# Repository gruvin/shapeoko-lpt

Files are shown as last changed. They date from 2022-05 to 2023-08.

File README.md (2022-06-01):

# Shapeoko UCCNC Upgrade

### Replacing [Shapeoko Pro XL](https://shop.carbide3d.com/collections/machines/products/shapeoko-pro-cnc-router?variant=33007028797501) basic stepper drivers and ditching GRBL in favour of advanced [UCCNC](https://cncdrive.com/UCCNC.html) Controller, using [UC100](https://cncdrive.com/UC100.html) USB interface to plug into this board.

## Why?

Mostly because I really like being able to pause, rewind, start, stop and see toolpaths in realtime. Call me old fashion. 

As a bonus, we get waaaaaay smoother, faster and generally more reliable stepper motors, using "proper" drivers.

## Features

Firstly, I didn't want to cut any wires ...

- Uses original Carbide3D Shapeoko power brick 24VDC @ 5A. (MOSFET switch and onboard 5V supply should handle double that V/A no problem.)
- Uses all original Shapeoko connectors for Power Switch (with blue LED), End Stops, BitSetter & BitZero. (An adapter board for the stepper motors is coming. The latter will be one each for the motor outputs on the stepper drivers.)

... etcetera ...
- Connects to your choice of "decent" stepper drivers

- Provides 24VDC/5A Charge Pump Switched power for drivers. Each of X/Y/Z ports has +5V/STEP/DIR/EN outputs (active low and Y1/Y2 are wired in parrallel or series. Your chpoice.)

- Built-in safety "charge pump" prevents 24VDC coming live until UCCNC is up and ready on the PC (can be bypassed with jumper.)

- VFD Spindle control with 0-10V speed control

- External 3 relay connector (4 if no charge pump). Relay 1 of 4 operates from EN (stepper enable). Relay 2 and 3 are connected to LPT P8 and P9 (Flood/Mist/Vacuum/Air.)

- Onboard 5VDC 1A supply.

- Input for **!! EMMERGENCY STOP !!** (normally closed switch.) Currently, the signal just goes to LPT P1, for your controller software (USCNC/Mach3) to deal with. Can use for that or Feed Hold if preferred.

## Status
### 2022-06-02 

First batch of assembled prototype PCBs were a bust due to both errors and having been obsoleted by lots of design changes since ordering them.

Trying to get a full week without making any chages before ordering a set of V2.0.

### KiCAD sneak peek, very much a work in progress ...

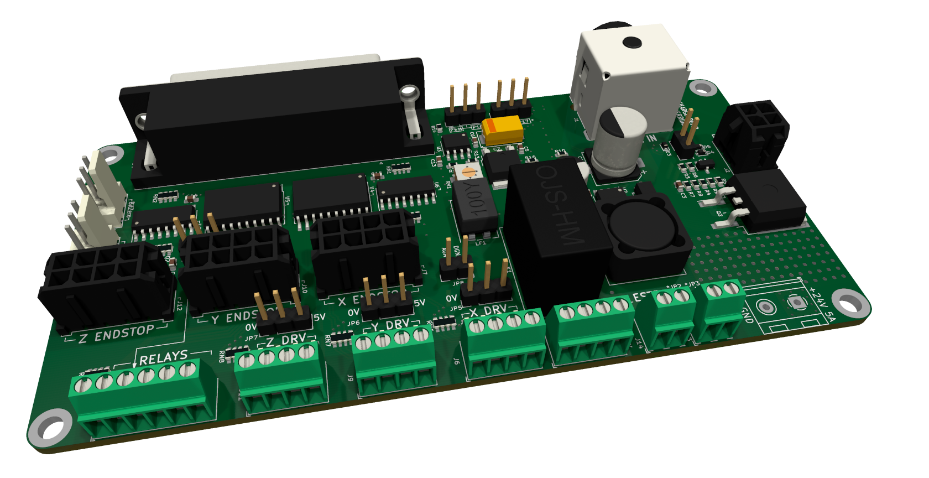
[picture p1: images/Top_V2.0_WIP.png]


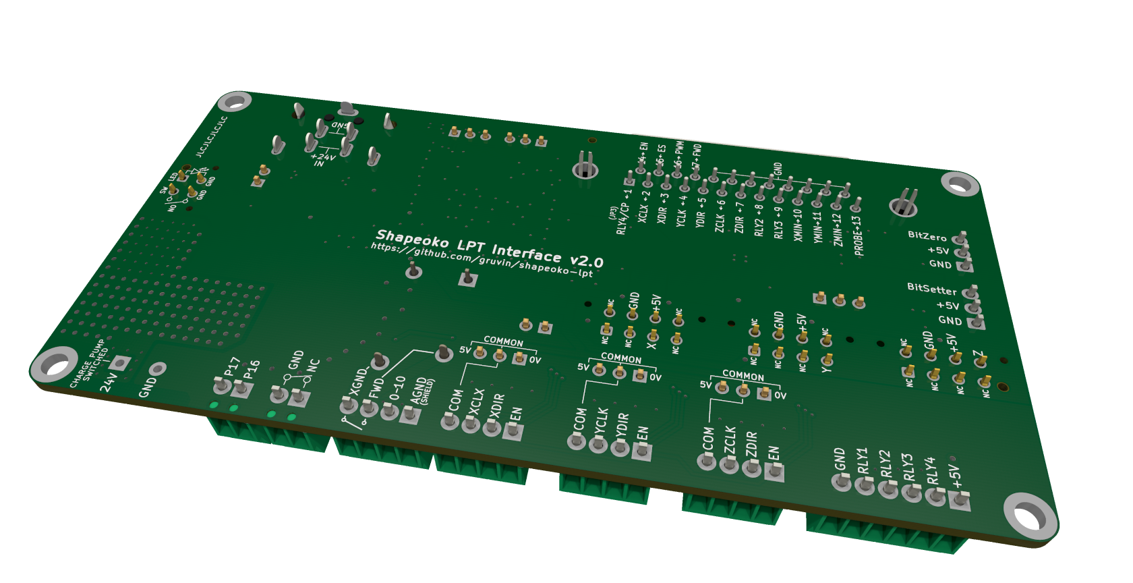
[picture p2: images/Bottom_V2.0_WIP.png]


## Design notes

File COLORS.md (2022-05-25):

# KiCAD 3D Viewer Custom Colors

## Solder Mask

### Purple
#370F80E7

### Emerald Green
#104624F7

## Other
Copper
#D99A6FFF

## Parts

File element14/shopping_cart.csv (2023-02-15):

Line No. | Order Code | Your Part No | Qty | Mfr Part No | Manufacturer Name | Manufacturer / Description | Availability | Unit Price (excl GST) | Line Price (excl GST)
1 | 1012247 |  | 5.0 | 43045-0412 | MOLEX | MOLEX Pin Header, With Polarizing Peg, Power, 3 mm, 2 Rows, 4 Contacts, Through Hole Straight | 30024 | 1.8900 | 9.45
2 | 1654450 |  | 3.0 | 43045-0814 | MOLEX | MOLEX Pin Header, Power, 3 mm, 2 Rows, 8 Contacts, Through Hole Straight, Micro-Fit 3.0 43045 | 4410 | 4.6500 | 13.95
3 | 2839851 |  | 1.0 | KPJX-4S-S | KYCON | KYCON High Power Connector, Through Hole, KPJX, Receptacle, 48 VDC, 7.5 A, PCB Mount, Through Hole | 3085 | 2.5900 | 2.59
4 | 2646350 |  | 1.0 | IRF9540SPBF | VISHAY | VISHAY Power MOSFET, P Channel, 100 V, 19 A, 0.2 ohm, TO-263AB, Surface Mount | 1484 | 4.3800 | 4.38
5 | 2527547 |  | 10.0 | CTBP5000/2 | CAMDENBOSS | CAMDENBOSS Wire-To-Board Terminal Block, 5 mm, 2 Ways, 22 AWG, 14 AWG, 1.5 mm², Screw | 5179 | 0.5280 | 5.28
6 | 2799102 |  | 1.0 | MAX5035BUSA+T | MAXIM INTEGRATED / ANALOG DEVICES | MAXIM INTEGRATED / ANALOG DEVICES Buck (Step Down), Switching Regulator, Fixed, 7.5V to 76V In, 5V/1A Out, 125kHz, NSOIC-8 | 5 | 6.1300 | 6.13
7 | 1635912 |  | 2.0 | 74477120 | WURTH ELEKTRONIK | WURTH ELEKTRONIK Power Inductor (SMD), 100 µH, 1.53 A, Shielded, 1.7 A, WE-PD, 12mm x 12mm x 6mm | 7979 | 3.3300 | 6.66
8 | 2836989 |  | 1.0 | MAL218397104E3 | VISHAY | VISHAY Hybrid Aluminium Electrolytic Capacitor, 68 µF, ± 20%, 50 V, Radial Can - SMD, 0.03 ohm | 1430 | 7.1500 | 7.15
9 | 2611386 |  | 2.0 | MCVVT035M221FB3L | MULTICOMP PRO | MULTICOMP PRO SMD Aluminium Electrolytic Capacitor, Radial Can - SMD, 220 µF, 35 V, 2000 hours @ 105°C, Polar | 504 | 0.3880 | 0.78
10 | 2507732 |  | 2.0 | EEEFK1V680SP | PANASONIC | PANASONIC SMD Aluminium Electrolytic Capacitor, Radial Can - SMD, 68 µF, 35 V, 0.36 ohm, 2000 hours @ 105°C | 4855 | 0.9200 | 1.84
11 | 2611399 |  | 5.0 | MCVVT050M221GB3L | MULTICOMP PRO | MULTICOMP PRO SMD Aluminium Electrolytic Capacitor, Radial Can - SMD, 220 µF, 50 V, 2000 hours @ 105°C, Polar | 2886 | 0.5480 | 2.74
12 | 1709948 |  | 20.0 | MC0603B103M500CT | MULTICOMP PRO | MULTICOMP PRO CERAMIC CAPACITOR 0.01UF, 50V, X7R, 20%, 0603 | 9703 | 0.0450 | 0.90
13 | 9402080 |  | 20.0 | CC0603KRX5R6BB105 | YAGEO | YAGEO SMD Multilayer Ceramic Capacitor, 1 µF, 10 V, 0603 [1608 Metric], ± 10%, X5R, CC Series | 918203 | 0.0270 | 0.54
14 | 432210 |  | 20.0 | CC0603KRX7R7BB104 | YAGEO | YAGEO SMD Multilayer Ceramic Capacitor, 0.1 µF, 16 V, 0603 [1608 Metric], ± 10%, X7R, CC Series | 695378 | 0.0300 | 0.60
15 | 3407110 |  | 10.0 | RRE07VSM6STR | ROHM | ROHM Small Signal Diode, Single, 600 V, 700 mA, 1.1 V, 2 A | 2850 | 0.6240 | 6.24

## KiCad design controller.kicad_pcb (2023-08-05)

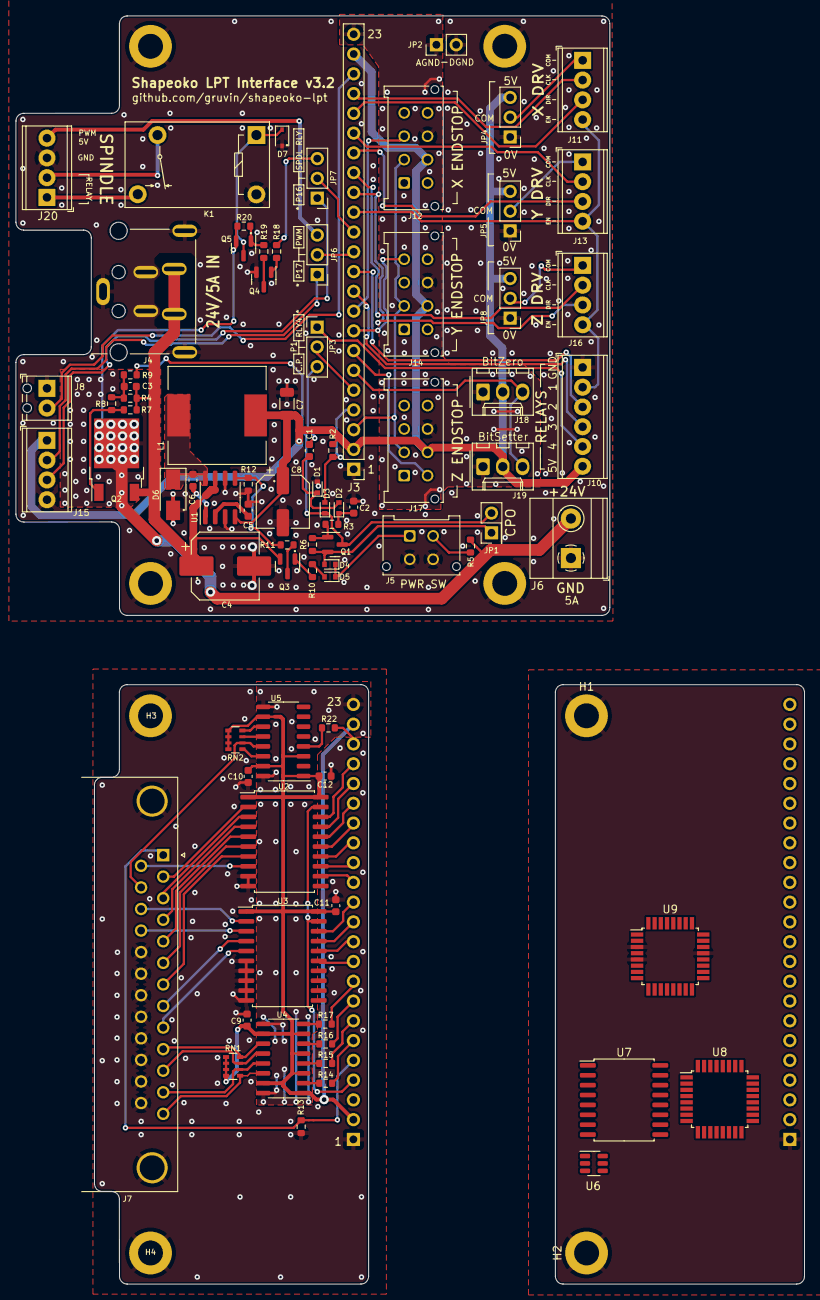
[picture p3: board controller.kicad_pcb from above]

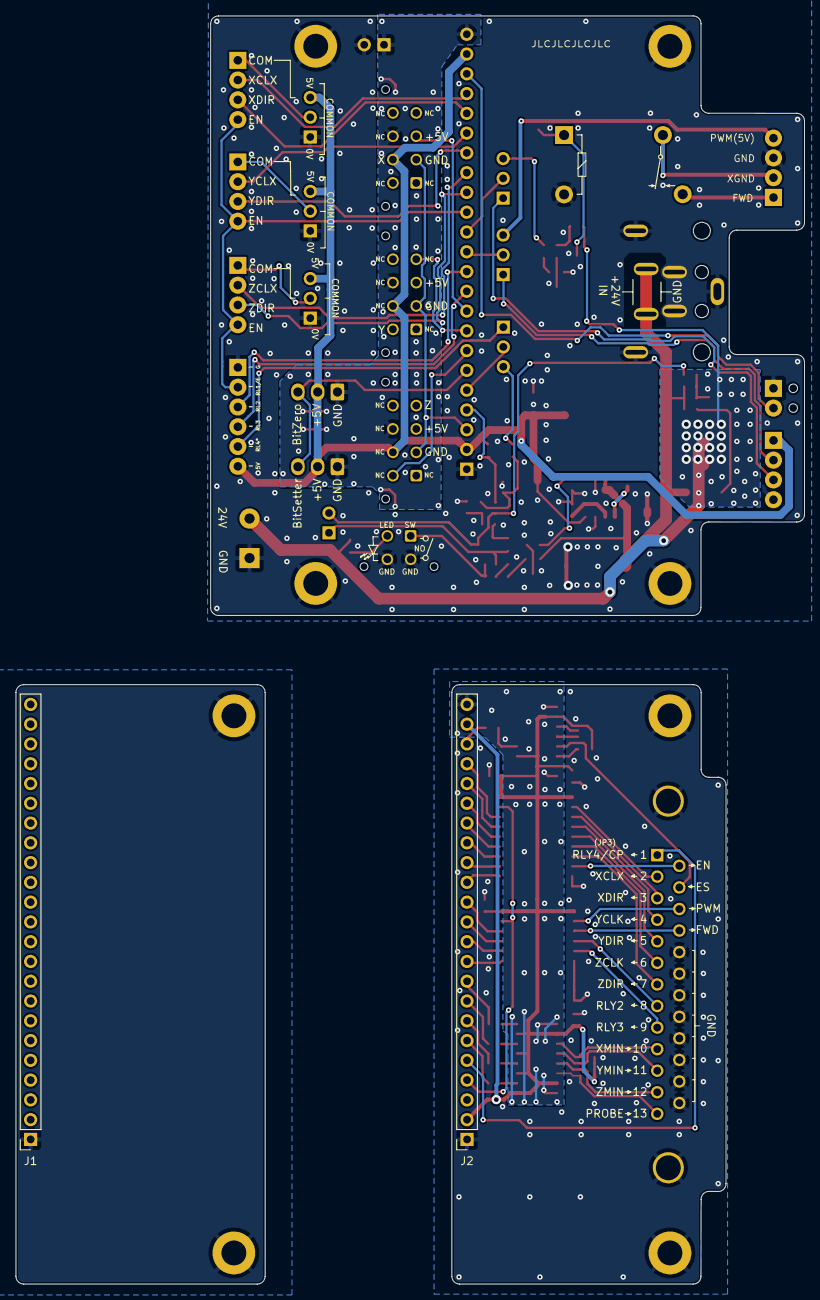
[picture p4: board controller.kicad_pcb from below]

Board: 2 copper layers, 101.3 x 162.9 mm, 100 parts (6 on the bottom side), 126 nets.

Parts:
C1, C5, C6, C9, C10, C11, C12: 100n/50V; C_0603_1608Metric
C2, C3: 1u/50V; C_0603_1608Metric
C4: 100u/35V; CP_Elec_8x10.5_DOT
C7: 22u/25V; C_1206_3216Metric
C8: 68u/35V; CP_Elec_6.3x7.7_DOT
D1, D2, D3, D4, D5: SDM20U40-7; D_SOD-523
D6: SS24A+; D_SMA_DOT
D7: BAT54JFILM; D_SOD-323_DOT
H1, H2, H3, H4, H5, H6, H7, H8: MountingHole_Pad; MountingHole_3.2mm_M3_ISO14580_Pad
J1, J2: Conn_01x06_Female; PinSocket_1x23_P2.54mm_Vertical
J3: Conn_01x022_Male; PinHeader_1x23_P2.54mm_Vertical
J4: KYCON_KPJX-4S-S
J5: MicroFit_2x02; Molex_Micro-Fit_3.0_43045-0412_2x02_P3.00mm_Vertical
J6: 24V/5A OUT; TerminalBlock_Phoenix_MKDS-1,5-2-5.08_1x02_P5.08mm_Horizont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
J7: DB25 FEMALE; DSUB-25_Male_Horizontal_P2.77x2.84mm_EdgePinOffset7.70mm_Ho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
J8: Phoenix MPT; TerminalBlock_Phoenix_MPT-0,5-2-2.54_1x02_P2.54mm_Horizontal
J10: Phoenix MPT; TerminalBlock_Phoenix_MPT-0,5-6-2.54_1x06_P2.54mm_Horizontal
J11, J13, J16, J20: Phoenix MPT; TerminalBlock_Phoenix_MPT-0,5-4-2.54_1x04_P2.54mm_Horizontal
J12, J14, J17: MicroFit_2x04; Molex_Micro-Fit_3.0_43045-0812_2x04_P3.00mm_Vertical
J15: JST_B2B-XH; TerminalBlock_Phoenix_MPT-0,5-4-2.54_1x04_P2.54mm_Horizontal
J18, J19: MLX_1x03; Molex_KK-254_AE-6410-03A_1x03_P2.54mm_Vertical
JP1: Jumper_2; PinHeader_2x01_P2.54mm_Vertical
JP2: GND_ISO; PinHeader_1x02_P2.54mm_Vertical
JP3, JP6, JP7: 1x03_2.54; PinHeader_1x03_P2.54mm_Vertical
JP4, JP5, JP8: Jumper_3; PinHeader_1x03_P2.54mm_Vertical
K1: OJS-SH-124HMF; Relay_SPST_OJS_24V_10A
L1: 100uH 1.5A+; L_12x12mm_H6mm
NT1: NetTie_2; NetTie-2_SMD_Pad0.3mm
NT22, NT25, NT26, NT27: DNI; NetTie-2_SMD_Pad0.3mm
NT23, NT24, NT28: DNI; NetTie-2_SMD_Pad1.0mm
Q1, Q4: BC847; SOT-23
Q2: FDD5614P; TO-252-2
Q3, Q5: BC857; SOT-23_DOT
R2, R7, R11, R13: 1M; R_0603_1608Metric
R3: 6K8; R_0603_1608Metric
R4, R12: 220K; R_0603_1608Metric
R5: 1K; R_0603_1608Metric
R6, R10: 130K; R_0603_1608Metric
R8: 680K; R_0603_1608Metric
R9: 330K; R_0603_1608Metric
R14, R15, R16, R17, R22: 330; R_0603_1608Metric
R18, R19: 5K6; R_0603_1608Metric
R20: 10K; R_0603_1608Metric
RN1, RN2: 1Kx4; R_Array_Convex_4x0603
U1: MAX5035BUSA; SOIC-8_3.9x4.9mm_P1.27mm
U2, U3: 74HC245; SOIC-20W_7.5x12.8mm_P1.27mm
U4, U5: ACSL-6310; SO-16_3.9x9.9mm_P1.27mm
U6: USBLC6-2SC6; SOT-23-6
U7: ADUM4160; SOIC-16W_7.5x10.3mm_P1.27mm
U8: ATmega16U2-A; TQFP-32_7x7mm_P0.8mm
U9: ATmega328P-A; TQFP-32_7x7mm_P0.8mm

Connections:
5V_nEN: D5.2 (A), R10.2
24V_IN: C3.1, C4.1, J4.1, J4.4, NT23.1, Q2.3 (S), R4.1, R7.2
24V_SAFE: J6.2, NT22.2, Q2.2 (D), Q5.2 (E), R20.1
+5V: J3.2, J3.22, J10.6, J12.6, J14.6, J15.1, J17.6, J18.2, J19.2, NT24.2, NT28.2, R2.2
+5VA: C9.1, C10.1, C11.1, C12.1, J1.2, J1.22, J2.2, J2.22, RN1.1 (R1.1), RN1.2 (R2.1), RN1.3 (R3.1), RN1.4 (R4.1), RN2.1 (R1.1), RN2.2 (R2.1), RN2.3 (R3.1), RN2.4 (R4.1), U2.1 (A->B), U2.20 (VCC), U3.1 (A->B), U3.20 (VCC), U4.1 (A1), U4.3 (A2), U4.5 (A3), U4.7 (A4), U4.10 (Vdd), U4.15 (Vdd), U5.1 (A1), U5.3 (A2), U5.5 (A3), U5.7 (A4), U5.10 (Vdd), U5.15 (Vdd), U9.4 (VCC), U9.6 (VCC), U9.18 (AVCC), U9.20 (AREF)
/Connectors & Jumpers/CHARGE_PUMP_OUT: C1.1, JP3.3 (B)
/Connectors & Jumpers/EN_IN: J3.14, J11.4, J13.4, J16.4, NT27.1
/Connectors & Jumpers/ESTOP_OUT: J3.21, J8.2
/Connectors & Jumpers/HOLD_OUT: J3.3, J12.2, J14.2, J17.2
/Connectors & Jumpers/P1_IN: J3.5, JP3.2 (C)
/Connectors & Jumpers/P16_IN: J3.13, JP7.2 (C)
/Connectors & Jumpers/P17_IN: J3.12, JP6.2 (C)
/Connectors & Jumpers/PROBE_OUT: J3.6, J18.3, J19.3
/Connectors & Jumpers/RELAY1: J10.2, NT27.2
/Connectors & Jumpers/RELAY2: J10.3, NT26.2
/Connectors & Jumpers/RELAY2_IN: J3.11, NT26.1
/Connectors & Jumpers/RELAY3: J10.4, NT25.2
/Connectors & Jumpers/RELAY3_IN: J3.10, NT25.1
/Connectors & Jumpers/RELAY4: J10.5, JP3.1 (A)
/Connectors & Jumpers/STP_5V: JP4.3 (B), JP5.3 (B), JP8.3 (B), NT28.1
/Connectors & Jumpers/VFD_FWD: J20.2, K1.5
/Connectors & Jumpers/VFD_PWM: J20.4, JP6.3 (B)
/Connectors & Jumpers/VFD_XGND: J20.1, K1.3
/Connectors & Jumpers/XCLK_IN: J3.20, J11.2
/Connectors & Jumpers/XDIR_IN: J3.19, J11.3
/Connectors & Jumpers/XMIN_OUT: J3.9, J12.3
/Connectors & Jumpers/X_COM: J11.1, JP4.2 (C)
/Connectors & Jumpers/X_P16_OUT: J15.3, JP7.1 (A)
/Connectors & Jumpers/X_P17_OUT: J15.2, JP6.1 (A)
/Connectors & Jumpers/YCLK_IN: J3.18, J13.2
/Connectors & Jumpers/YDIR_IN: J3.17, J13.3
/Connectors & Jumpers/YMIN_OUT: J3.8, J14.4
/Connectors & Jumpers/Y_COM: J13.1, JP5.2 (C)
/Connectors & Jumpers/ZCLK_IN: J3.16, J16.2
/Connectors & Jumpers/ZDIR_IN: J3.15, J16.3
/Connectors & Jumpers/ZMIN_OUT: J3.7, J17.5
/Connectors & Jumpers/Z_COM: J16.1, JP8.2 (C)
/GRBL Interface/HOLD_IN: J1.3, U9.24 (PC1)
/GRBL Interface/P2_OUT: J1.20, U9.32 (PD2)
/GRBL Interface/P3_OUT: J1.19, U9.9 (PD5)
/GRBL Interface/P4_OUT: J1.18, U9.1 (PD3)
/GRBL Interface/P5_OUT: J1.17, U9.10 (PD6)
/GRBL Interface/P6_OUT: J1.16, U9.2 (PD4)
/GRBL Interface/P7_OUT: J1.15, U9.11 (PD7)
/GRBL Interface/P8_OUT: J1.11, U9.26 (PC3)
/GRBL Interface/P9_OUT: J1.10, U9.27 (PC4)
/GRBL Interface/P10_IN: J1.9, U9.13 (PB1)
/GRBL Interface/P11_IN: J1.8, U9.14 (PB2)
/GRBL Interface/P12_IN: J1.7, U9.16 (PB4)
/GRBL Interface/P13_IN: J1.6, U9.28 (PC5)
/GRBL Interface/P14_OUT: J1.14, U9.12 (PB0)
/GRBL Interface/P15_IN: J1.21, U9.23 (PC0)
/GRBL Interface/P16_OUT: J1.13, U9.17 (PB5)
/GRBL Interface/P17_OUT: J1.12, U9.15 (PB3)
/LPT Interface/P1_IN: J7.1, NT1.1, R13.1
/LPT Interface/P1_OUT: J2.5, NT1.2
/LPT Interface/P2_IN: J7.2, U2.2 (A0)
/LPT Interface/P2_OUT: J2.20, U2.18 (B0)
/LPT Interface/P3_IN: J7.3, U2.3 (A1)
/LPT Interface/P3_OUT: J2.19, U2.17 (B1)
/LPT Interface/P4_IN: J7.4, U2.4 (A2)
/LPT Interface/P4_OUT: J2.18, U2.16 (B2)
/LPT Interface/P5_IN: J7.5, U2.5 (A3)
/LPT Interface/P5_OUT: J2.17, U2.15 (B3)
/LPT Interface/P6_IN: J7.6, U2.6 (A4)
/LPT Interface/P6_OUT: J2.16, U2.14 (B4)
/LPT Interface/P7_IN: J7.7, U2.7 (A5)
/LPT Interface/P7_OUT: J2.15, U2.13 (B5)
/LPT Interface/P8_IN: J7.8, U3.4 (A2)
/LPT Interface/P8_OUT: J2.11, U3.16 (B2)
/LPT Interface/P9_IN: J7.9, U3.5 (A3)
/LPT Interface/P9_OUT: J2.10, U3.15 (B3)
/LPT Interface/P10_IN: J2.9, R17.2
/LPT Interface/P10_OUT: J7.10, RN1.8 (R1.2), U4.11 (O1)
/LPT Interface/P11_IN: J2.8, R16.2
/LPT Interface/P11_OUT: J7.11, RN1.7 (R2.2), U4.12 (O1)
/LPT Interface/P12_IN: J2.7, R15.2
/LPT Interface/P12_OUT: J7.12, RN1.6 (R3.2), U4.13 (O1)
/LPT Interface/P13_IN: J2.6, R14.2
/LPT Interface/P13_OUT: J7.13, RN1.5 (R4.2), U4.14 (O1)
/LPT Interface/P14_IN: J7.14, U2.8 (A6)
/LPT Interface/P14_OUT: J2.14, U2.12 (B6)
/LPT Interface/P15_IN: J2.21, R22.2
/LPT Interface/P15_OUT: J7.15, RN2.6 (R3.2), U5.13 (O1)
/LPT Interface/P16_IN: J7.16, U3.2 (A0)
/LPT Interface/P16_OUT: J2.13, U3.18 (B0)
/LPT Interface/P17_IN: J7.17, U3.3 (A1)
/LPT Interface/P17_OUT: J2.12, U3.17 (B1)
/LPT Interface/nCE_IN: J2.4, U2.19 (CE), U3.19 (CE)
/Power/PLED: J5.2, R5.1
/Power/Q1_B: Q1.1 (B), R3.2, R6.1
/Power/Q1_C: D3.1 (K), JP1.2 (B), Q1.3 (C), R9.2
/Power/Q1_E: D4.2 (A), JP1.1 (A), Q1.2 (E), R6.2
/Power/U2_BST: C6.1, U1.1 (BST)
/Power/U2_FB: C7.2, C8.1, L1.2, NT24.1, U1.4 (FB)
/Power/U2_LX: C6.2, D6.1 (K), L1.1, U1.8 (LX)
/Power/U2_ON_nOFF: R11.1, R12.1, U1.5 (ON/~OFF)
/Power/U2_VD: C5.1, U1.2 (VD)
/Power/U2_VIN: NT23.2, Q3.2 (E), U1.7 (VIN)
/Power/nCE_OUT: D3.2 (A), J3.4, R2.1
GND: C2.2, C4.2, C5.2, C7.1, C8.2, D1.2 (A), D6.2 (A), D7.2 (A), H5.1, H6.1, H7.1, H8.1, J3.1, J4.2, J4.3, J4.SH, J5.3, J5.4, J6.1, J8.1, J10.1, J15.4, J20.3, JP2.2 (B), JP4.1 (A), JP5.1 (A), JP8.1 (A), K1.1, Q4.2 (E), R12.2, U1.3 (SGND), U1.6 (GND)
GND1: C9.2, C10.2, C11.2, C12.2, H1.1, H2.1, H3.1, H4.1, J1.1, J2.1, J7.0 (PAD), J7.18, J7.19, J7.20, J7.21, J7.22, J7.23, J7.24, J7.25, R13.2, U2.9 (A7), U2.10 (GND), U3.6 (A4), U3.7 (A5), U3.8 (A6), U3.9 (A7), U3.10 (GND), U9.3 (GND), U9.5 (GND), U9.21 (GND)
GND2: J1.23, J2.23, U4.9 (GND), U4.16 (GND), U5.9 (GND), U5.16 (GND)
GND3: U7.2 (GND1), U7.8 (GND1)
GNDA: J3.23, J12.7, J14.7, J17.7, J18.1, J19.1, JP2.1 (A)
unnamed: C1.2, D1.1 (K), D2.2 (A)
unnamed: C2.1, D2.1 (K), R3.1
unnamed: C3.2, R4.2, R8.1, R9.1
unnamed: D4.1 (K), D5.1 (K), J5.1
unnamed: D7.1 (K), K1.6, Q5.3 (C)
unnamed: JP7.3 (B), R18.2
unnamed: NT22.1, R5.2
unnamed: Q2.1 (G), R7.1, R8.2
unnamed: Q3.1 (B), R10.1
unnamed: Q3.3 (C), R11.2
unnamed: Q4.1 (B), R18.1
unnamed: Q4.3 (C), R19.2
unnamed: Q5.1 (B), R19.1, R20.2
unnamed: R14.1, U4.2 (C1)
unnamed: R15.1, U4.4 (C2)
unnamed: R16.1, U4.6 (C3)
unnamed: R17.1, U4.8 (C4)
unnamed: R22.1, U5.4 (C2)
unnamed: RN2.8 (R1.2), U5.11 (O1)
unnamed: RN2.7 (R2.2), U5.12 (O1)
unnamed: RN2.5 (R4.2), U5.14 (O1)

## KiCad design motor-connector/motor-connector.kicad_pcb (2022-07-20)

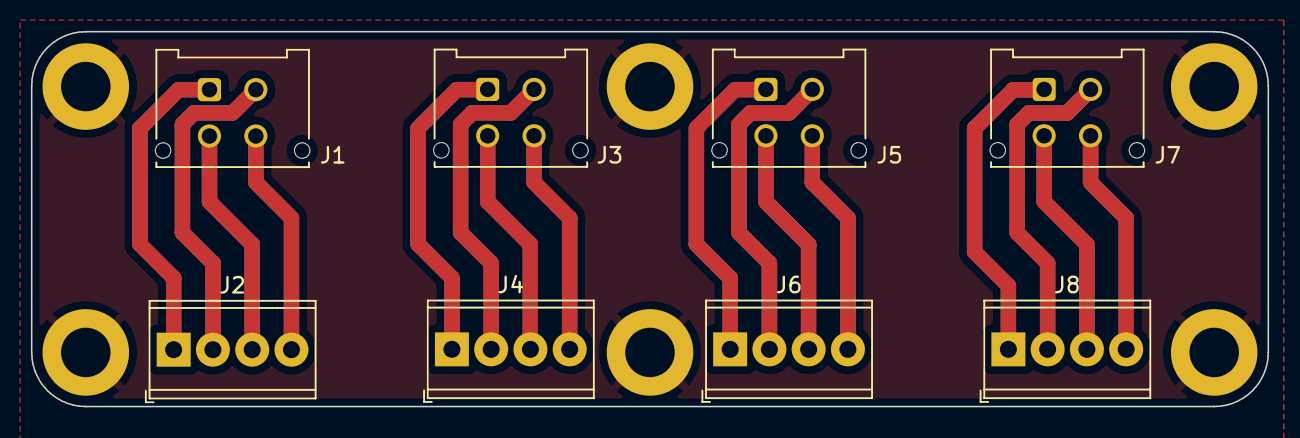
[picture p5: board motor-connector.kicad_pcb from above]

Board: 2 copper layers, 80.0 x 24.2 mm, 14 parts (0 on the bottom side), 17 nets.

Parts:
H1, H2, H3, H4, H5, H6: MountingHole_Pad; MountingHole_3.2mm_M3_DIN965_Pad
J1, J3, J5, J7: Conn_02x02_Top_Bottom; Molex_Micro-Fit_3.0_43045-0412_2x02_P3.00mm_Vertical
J2, J4, J6, J8: Conn_01x04; TerminalBlock_Phoenix_MPT-0,5-4-2.54_1x04_P2.54mm_Horizontal

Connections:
GND: H1.1, H2.1, H3.1, H4.1, H5.1, H6.1
unnamed: J1.1, J2.1
unnamed: J1.2, J2.2
unnamed: J1.3, J2.3
unnamed: J1.4, J2.4
unnamed: J3.1, J4.1
unnamed: J3.2, J4.2
unnamed: J3.3, J4.3
unnamed: J3.4, J4.4
unnamed: J5.1, J6.1
unnamed: J5.2, J6.2
unnamed: J5.3, J6.3
unnamed: J5.4, J6.4
unnamed: J7.1, J8.1
unnamed: J7.2, J8.2
unnamed: J7.3, J8.3
unnamed: J7.4, J8.4

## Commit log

2022-05-14 Much to do about OCD power distribution. (Removed all loop 'antennas' and balanced transmission lines..)
    [controller.kicad_pcb, controller.kicad_sch, power.kicad_sch]
2022-05-14 Some more decoupling caps and routing optimizations.
    [controller.kicad_pcb, controller.kicad_sch, lpt.kicad_sch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]
2022-05-15 Lots of changes and errors fixed. Updated vanity images.
    [conn.kicad_sch, controller.kicad_pcb, controller.kicad_sch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]
2022-05-15 Probe connectors wired wrong. Improved 5V buck reg layout.
    [conn.kicad_sch, controller.kicad_pcb, controller.kicad_sch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]
2022-05-16 Added LEDs (more coming). Changes to charge pump and related power switching.
    [conn.kicad_sch, controller.kicad_pcb, controller.kicad_sch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]
2022-05-16 Forgot R1 and more NT fun.
    [conn.kicad_sch, controller.kicad_pcb, controller.kicad_sch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]
2022-05-17 Resistor networks changed to 0603 'cause JLCPCB has those as 'basic parts' & aunch of tweaks. (WIP)
    [conn.kicad_sch, controller.kicad_pcb, controller.kicad_sch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]
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2022-05-17 Scary file corruption turns out to be just bugs in eschema.
    [conn.kicad_sch, controller.kicad_pcb, controller.kicad_sch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]
2022-05-17 Removed 'Element14' field from all sch/pcb components
    [conn.kicad_sch, controller.kicad_pcb, controller.kicad_sch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]
2022-05-18 Reworked PSU control scheme (schematic only.)
    [conn.kicad_sch, controller.kicad_pcb, controller.kicad_sch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]
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2022-05-18 Change share/_footprints to share/module with new alias '-Project'
    [conn.kicad_sch, controller.kicad_pcb, controller.kicad_sch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]
2022-05-18 Much to do about power
    [conn.kicad_sch, controller.kicad_pcb, controller.kicad_sch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]
2022-05-19 Routed power switching changes.
    [conn.kicad_sch, controller.kicad_pcb, controller.kicad_sch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]
2022-05-19 More power supply and 5A ground return routing optimization.
    [controller.kicad_pcb, controller.kicad_sch, lpt.kicad_sch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]
2022-05-20 Tweaks and JLCPCB LCSC field name changes.
    [conn.kicad_sch, controller.kicad_pcb, controller.kicad_sch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]
2022-05-20 Added 100n extra decoupling cap to PWM 12V reg.
    [conn.kicad_sch, controller.kicad_pcb, controller.kicad_sch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]
2022-05-20 I'm soooo done with this board! :/
    [conn.kicad_sch, controller.kicad_pcb, controller.kicad_sch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]
2022-05-21 Some fixes .... and ... a MAJOR fuck up on the power connector, after the board went into production already.
    [conn.kicad_sch, controller.kicad_pcb, controller.kicad_sch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]
2022-05-21 Corrected unbelievably DUMB ballsup on input power connector.
    [conn.kicad_sch, controller.kicad_pcb, controller.kicad_sch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]
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2022-05-22 More OCD hours really. I need to stop. It's getting stupid. :P
    [controller.kicad_pcb]
2022-05-22 DRC checks. Tagging as V1.0 'actual'
    [conn.kicad_sch, controller.kicad_pcb, controller.kicad_sch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]
2022-05-22 Prepping JLCPCB order for v1.1 assembled boards.
    [controller-B_Cu.gbr, controller-B_Mask.gbr, controller-B_Paste.gbr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]
2022-05-22 JLCPCB Order Placed for JLCPCB_V1.1_FROZEN/.
    [bom-jlcpcb.csv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]
2022-05-23 Lost the top layer ground plane. Got sick of being in Via Hell.
    [conn.kicad_sch, controller.kicad_pcb, controller.kicad_sch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]
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2022-05-24 Unfinished 5V buck routing optimization.
    [controller.kicad_pcb]
2022-05-25 Tweaks & recorded custom 3D Viewer colors.
    [controller.kicad_pcb]
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2022-05-27 Fixed stupid error with LED circuit. (LED are lights, yes but they only turn on when current is going a certain direction. Duh. LOL)
    [conn.kicad_sch, controller.kicad_pcb, controller.kicad_sch]
2022-05-28 Mostly groundplane declutter and loop removal.
    [conn.kicad_sch, controller.kicad_pcb, controller.kicad_sch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]
2022-05-28 More ground plane clearance/optimization.
    [controller.kicad_pcb, power.kicad_sch]
2022-05-29 Moving charge pump 15KHz input closer to source,
    [controller.kicad_pcb, controller.kicad_sch, power.kicad_sch]
2022-05-31 Fixed opto-isolator wrong part and added jumper to isolate A/DGNDs.
    [conn.kicad_sch, controller.kicad_pcb, controller.kicad_sch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]
2022-05-31 Chnaged opto-couplers to 3-ch versions. Cheaper and less waste[.|?]
    [conn.kicad_sch, controller.kicad_pcb, controller.kicad_sch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]
2022-06-01 Fixed yesterday's fix. Changed relay layout to allow 3A max terminal current, actually. Also changed VFD 0-10V PCB Farraday shield to reference VFD AGND instead of local GND.
    [conn.kicad_sch, controller.kicad_pcb, controller.kicad_sch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]
2022-06-01 Tidied up F.Fab and some silk screen. Added back 2 missing tooling holes.
    [controller.kicad_pcb]
2022-06-01 Part supply references wip.
    [conn.kicad_sch, controller.kicad_pcb, controller.kicad_sch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]
2022-06-01 WIP: Changing to terminal blocks for stepper, relay and VFD ports.
    [conn.kicad_sch, controller.kicad_pcb, controller.kicad_sch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]
2022-06-01 Completed change to screw terminal blocks. (P16/17 remains JST.)
    [conn.kicad_sch, controller.kicad_pcb, controller.kicad_sch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]
2022-06-01 Changed name to Shapeoko LPT Interface v2.0
    [conn.kicad_sch, controller.kicad_pcb, controller.kicad_sch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]
2022-06-01 'Fixed' CAM/Grid origins.
    [controller.kicad_pcb]
2022-06-02 Silkscreen errors
    [controller.kicad_pcb]
2022-06-02 Completed element14 part codes
    [conn.kicad_sch, controller.kicad_pcb, controller.kicad_sch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]
2022-06-03 Change and reposition JP16/17 connector to screw terminal.
    [conn.kicad_sch, controller.kicad_pcb, controller.kicad_sch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]
2022-06-04 Moved LF1 to location afforded by new relay position.
    [conn.kicad_sch, controller.kicad_pcb]
2022-06-04 Minor silk tweaks. Update vanity images.
    [controller.kicad_pcb]
2022-06-04 Moved LPT left to protrude just over the PCB edge. Moved power connector inward to increase 24V/GND clearance.
    [controller.kicad_pcb]
2022-06-15 V2.1 after errors found on physical V2.0 boards. sigh
    [conn.kicad_sch, controller.kicad_pcb, power.kicad_sch]
2022-06-16 'Final' tidy-up before trying physical boards production, yet again. Frankly, this is getting ridiculous. Never made so many mistakes on such a simple board. Getting too old? (51)
    [controller.kicad_pcb]
2022-07-08 Correct Q1 pin muddle.
    [controller.kicad_pcb, power.kicad_sch]
2022-07-08 Correct Q5 pin muddle.
    [controller.kicad_pcb, controller.kicad_sch, lpt.kicad_sch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]
2022-07-08 Charge pump signal re-routed.
    Funny how the CP signal can't get through if /CE not asserted but /CE can only be asserted if the charge pump signal present. Oops. :/
    [controller.kicad_pcb, controller.kicad_sch, lpt.kicad_sch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]
2022-07-08 Corrected J2 pinout
    [controller.kicad_pcb, lpt.kicad_sch, power.kicad_sch]
2022-07-09 Fixed all three endstop pinout errors. :/
    [conn.kicad_sch, controller.kicad_pcb, controller.kicad_sch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]
2022-07-09 Add production files for JLCPCB_V3.0_FROZEN
    [controller-B_Cu.gbr, controller-B_Mask.gbr, controller-B_Paste.gbr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]
2022-07-09 Added fab plot to production files. Bumped PCB version to 3.1.
    [controller-B_Cu.gbr, controller-B_Fab.gbr, controller-B_Mask.gbr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]
2022-07-16 Added 1GW and 3FW part marking to values of the bp transistors.
    [controller.kicad_pcb]
2022-07-20 Added motor / driver interface PCBs
    [driver-connector.kicad_pcb, driver-connector.kicad_sch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]
2023-02-13 Two board version taking shape
    [conn.kicad_sch, controller.kicad_pcb, controller.kicad_sch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]
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2023-02-24 MILESTONE: Shrinkage Tk II
    [conn.kicad_sch, controller.kicad_pcb]
2023-02-24 MILESTONE: Shrinkage Tk II -- Added two more mouonting holes
    [controller.kicad_pcb, controller.kicad_sch]
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2023-02-28 MILSTONE: Production Candidate PC1
    [controller.kicad_pcb]
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2023-07-06 Optical isolator input current (10mA not 3mA) and wiring error fixed.
    [conn.kicad_sch, controller.kicad_pcb, controller.kicad_sch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]
2023-07-07 Multiple flaws resolved
    [conn.kicad_sch, controller.kicad_pcb, controller.kicad_sch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]
2023-07-09 Oh ... just a few more fuckups fixed
    [conn.kicad_sch, controller.kicad_pcb, controller.kicad_sch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]
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
